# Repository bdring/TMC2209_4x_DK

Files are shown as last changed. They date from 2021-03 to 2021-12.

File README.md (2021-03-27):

## TMC2209 4 Axis Grbl_ESP32 CNC Controller

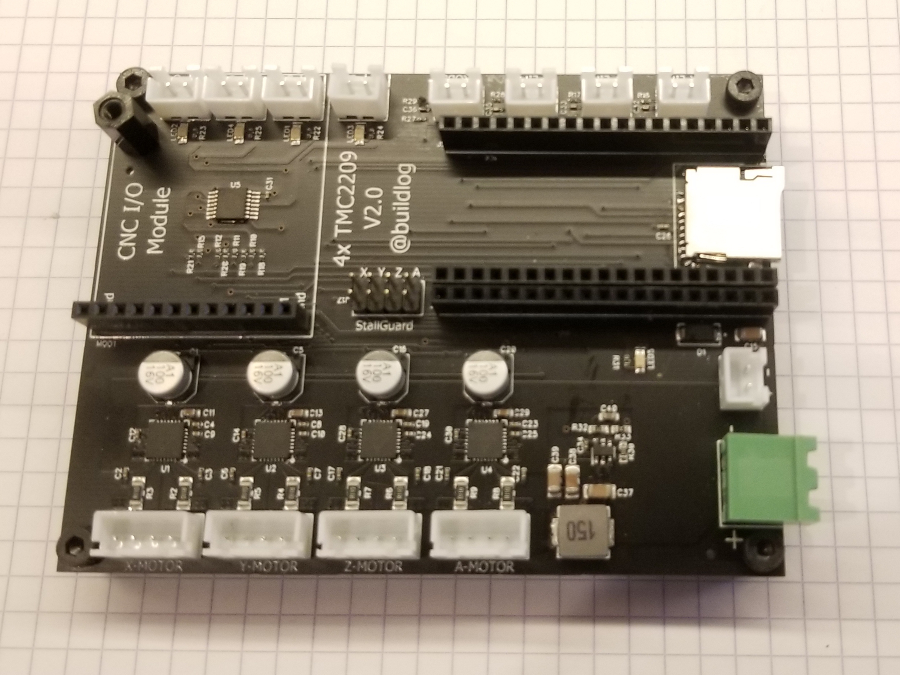
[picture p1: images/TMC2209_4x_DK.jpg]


This is a simple to set up and use CNC controller with 4 built in Trinamic TMC2209 stepper motor drivers. It is designed to run [Grbl_ESP32 firmware](https://github.com/bdring/Grbl_Esp32).

### Standard ESP32 Dev Kit Socket

The controller uses a standard ESP32 dev kit socket for module in the 2x19 format. It has an extra socket to allow the use of 0.9" wide and 1.0" wide versions.

### TMC2209 Drivers

These are very strong and super quiet stepper motor drivers. The firmware is in full control of the drivers. This allows you to set things like microstepping level and currents without jumpers and potentiometers. Sensorless end stops are supported. There are interactive tuning features to help set this up.

The 4 drivers can be set up for XYZA axes or any axis can be ganged for XYYZ type machines. 

### Inputs

There are 4 inputs. They are labeled for XY & Z limit limit switches and a probe, but they can be used for any type of input, such as XYZA or XYZ plus feed hold, etc.

### Outputs 

There are 4 outputs built into the controller. These are level shifted to 5V and can source or sink up to 25mA.  These can be used for spindle or laser PWMs. They can also be used to drive relay circuits. 

### CNC Output Modules.

The 4 outputs mentioned above are also wired to a standard CNC output module socket. This allows the use of many specialized modules, like RS485, 0-10V, Relays, High current MOSFETs, etc. This gives a lot of flexibility to this controller. Since the I/O for the modules is also wired to the built in outputs, you cannot use them independtly. 

Supported modules.

- [RS485 Modbus module for VFD spindles](https://github.com/bdring/6-Pack_CNC_Controller/wiki/RS485-Modbus-Module)
- [0-10V spindle module](https://github.com/bdring/6-Pack_CNC_Controller/wiki/0-10V-Output-Module)
- [Quad MOSFET module](https://github.com/bdring/6-Pack_CNC_Controller/wiki/Quad-MOSFET-Module)
- [Relay module](https://github.com/bdring/6-Pack_CNC_Controller/wiki/Relay-Module)
- [RC servo and BESC motor module](https://github.com/bdring/6-Pack_CNC_Controller/wiki/RC-Servo-BESC-CNC-I-O-Module)

### Micro SD Card

There is a micro SD socket. This allows gcode to be run without connected device.

### Laser Power Connector

There is a an extra connector that simply outputs the main power on a 2 terminal connector. This would typically used to power a low power laser module.

### Input Voltage

There is a pluggable terminal block for the input voltage. This is limited to 12V on version 2.0. Future versions will support 12V-24V.

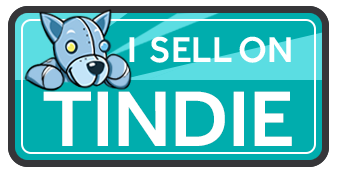
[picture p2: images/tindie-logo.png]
[](https://www.tindie.com/products/33366583/tmc2209-4-axis-grbl_esp32-cnc-controller/)

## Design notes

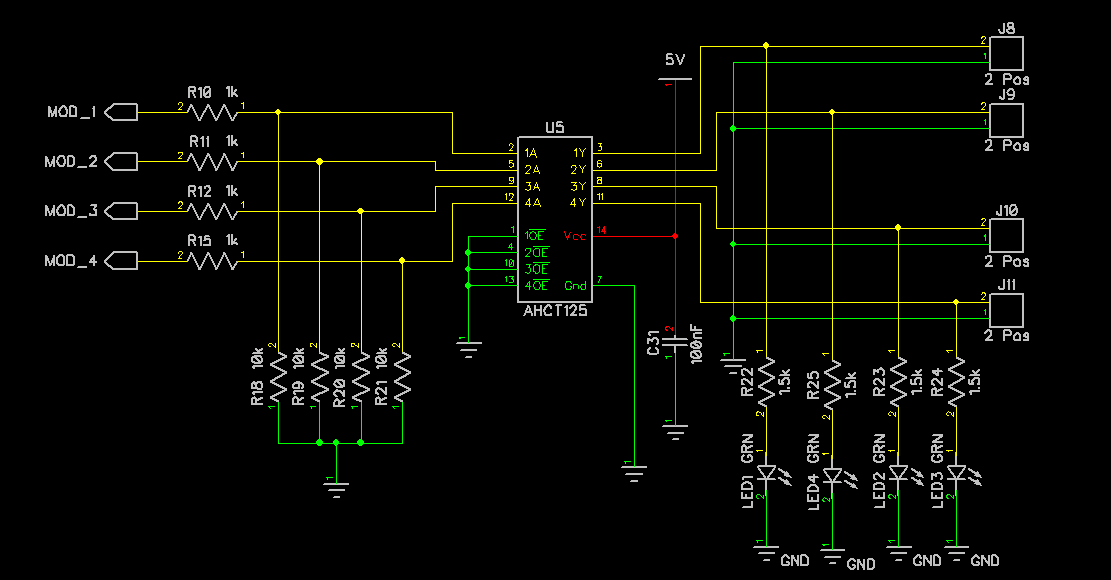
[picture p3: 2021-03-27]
images/5v_out_schematic.png

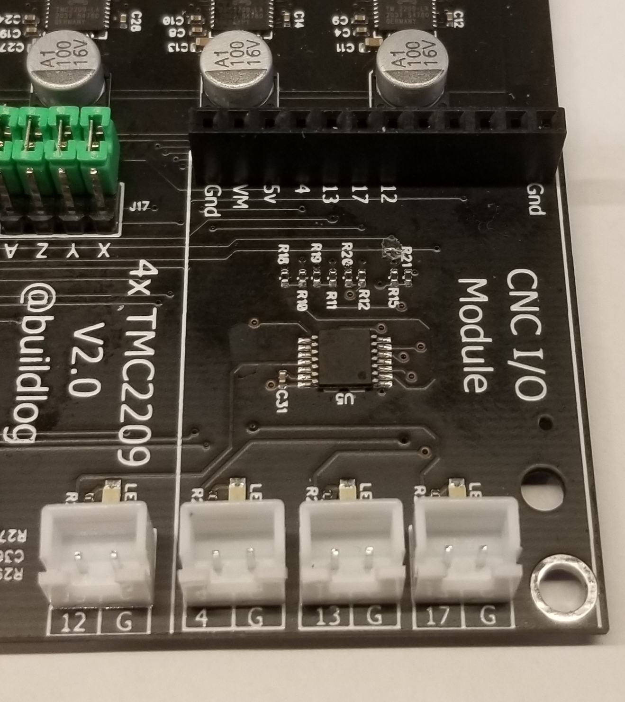
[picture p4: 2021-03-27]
images/output_pin_nums.jpg

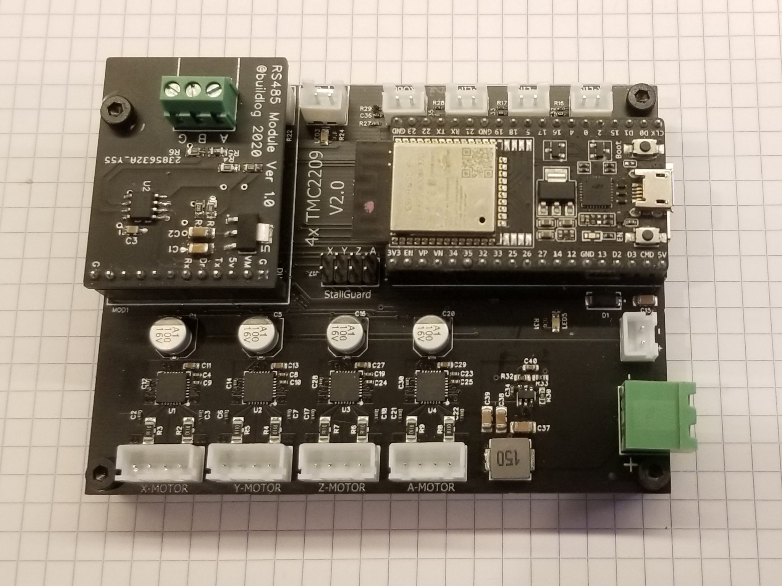
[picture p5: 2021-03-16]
images/TMC2209_4x_DK_Modules.jpg

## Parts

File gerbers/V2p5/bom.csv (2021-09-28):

RefDes | Quantity | Value | Name | Pattern | Manufacturer | MFG P/N | Source
C1, C5, C16, C20 | 4 | 100uF 35V | POL_100uF_35V EEEFK1V101XP | CaP_Elec_SMD_6.6x7.8 | PANASONIC | EEEFK1V101XP | https://lcsc.com/product-detail/Aluminum-Electrolytic-Capacitors-SMD_PANASONIC-EEEFK1V101XP_C178560.html
C2, C3, C4, C6, C7, C8, C12, C14, C17, C18, C19, C21, C22, C23, C26, C28, C30, C31, C32, C33, C34, C35, C36 | 23 | 100nF | NP_100nF_50V_0402 | CAP_0402_N | Samsung Electro-Mechanics | CL05B104KB54PNC | https://lcsc.com/product-detail/Others_Samsung-Electro-Mechanics_CL05B104KB54PNC_Samsung-Electro-Mechanics-CL05B104KB54PNC_C307331.html
C9, C10, C24, C25 | 4 | 22nF | NP_22nF_50V_0402 | CAP_0402_N | Samsung Electro-Mechanics | CL05B223KB5NNNC | https://lcsc.com/product-detail/Others_Samsung-Electro-Mechanics-CL05B223KB5NNNC_C337699.html
C11, C13, C27, C29 | 4 | 4.7uF | 4.7uF_25V_0603 | CAP_0603 | Samsung Electro-Mechanics | CL10A475KA8NQNC | https://lcsc.com/product-detail/Multilayer-Ceramic-Capacitors-MLCC-SMD-SMT_SAMSUNG_CL10A475KA8NQNC_4-7uF-475-10-25V_C69335.html
C15, C37 | 2 | 10uF 35V | NP_10uF_35V_1206 | CAP_1206 | Taiyo Yuden | GMK316BJ106KL-T | https://lcsc.com/product-detail/Multilayer-Ceramic-Capacitors-MLCC-SMD-SMT_Taiyo-Yuden-GMK316BJ106KL-T_C92797.html
C38, C39 | 2 | 22uF | NP_22uF_6.3V_1206 | CAP_1206 | Taiyo Yuden | JMK316BJ226KL-T | https://lcsc.com/product-detail/Multilayer-Ceramic-Capacitors-MLCC-SMD-SMT_TAIYO-YUDEN_JMK316BJ226KL-T_22uF-226-10-6-3V_C92791.html
C40 | 1 | 100pF | NP_100pF_50V_0603 | CAP_0603 | Walsin Tech Corp | 0603B101K500CT | https://lcsc.com/product-detail/Multilayer-Ceramic-Capacitors-MLCC-SMD-SMT_Walsin-Tech-Corp-0603B101K500_C123499.html
D1 | 1 | 40V 3A | Schottkey_40V_3A_DO-214AC | b340a-13-f | Diodes Incorporated | B340A-13-F | https://lcsc.com/product-detail/Schottky-Barrier-Diodes-SBD_DIODES_B340A-13-F_B340A-13-F_C85098.html
J1, J2, J6, J7 | 4 | 4P | XH-4A | B4B-XH-AM | BOOMELE(Boom Precision Elec) | C37815 | https://lcsc.com/product-detail/Wire-To-Board-Wire-To-Wire-Connector_BOOMELE-Boom-Precision-Elec-XH-4A_C37815.html
J3, J4, J5 | 3 | 19S | HDR Socket 1x19 0.1 | HDR-1x19 | Popular Products About LCSC | C319202 | https://lcsc.com/product-detail/Lack-of-specifications_BOOMELE-Boom-Precision-Elec-C319202_C319202.html
J8, J9, J10, J11, J12, J13, J14, J15, J16 | 9 | 2 Pos | B2B-XH-AM | B2B-XH-AM | JST | B2B-XH-AM(LF)(SN) | https://lcsc.com/product-detail/Wire-To-Board-Wire-To-Wire-Connector_JST-Sales-America-B2B-XH-AM-LF-SN_C161869.html
J17 | 1 | 2x4P | Header_2x4P | Header_2x4P 0.1 | Ckmtw(Shenzhen Cankemeng | C124386 | https://lcsc.com/product-detail/Pin-Header-Female-Header_Ckmtw-Shenzhen-Cankemeng-C124386_C124386.html
L1 | 1 | 15uH | 15uH_MWSA0603S | Inductor_MWSA0603S | Sunlord | MWSA0603S-150MT | https://lcsc.com/product-detail/Power-Inductors_Sunlord-MWSA0603S-150MT_C408452.html
LED1, LED2, LED3, LED4, LED5 | 5 | GRN | LED_GRN_0805 (Foshan) | LED_0805 | Foshan NationStar Optoelectronics | NCD0805G1 | https://lcsc.com/product-detail/Light-Emitting-Diodes-LED_Foshan-NationStar-Optoelectronics-NCD0805G1_C84260.html
MH1, MH2, MH3, MH4 | 4 |  | Mounting_hole_M3.7 | M4 Mounting Hole
MOD1 | 1 | 1x12 Socket | CNC_Module_Socket | CNC_Module_V3 | CJT(Changjiang Connectors) | A2541HWV-12P | https://lcsc.com/product-detail/Pin-Header-Female-Header_CJT-Changjiang-Connectors-A2541HWV-12P_C225509.html
R1, R13, R14, R18, R19, R20, R21, R26, R27 | 9 | 10k | 10k_0402 | RES_0402_N | YAGEO | RC0402FR-0710KL | https://lcsc.com/product-detail/Chip-Resistor-Surface-Mount_YAGEO-RC0402FR-0710KL_C60490.html
R2, R3, R4, R5, R6, R7, R8, R9 | 8 | 0.11R | 0.11R_1206 | RES_1206 | Uniroyal Elec | 1206W4F110LT5E | https://lcsc.com/product-detail/Chip-Resistor-Surface-Mount_UNI-ROYAL-Uniroyal-Elec-1206W4F110LT5E_C82532.html
R10, R11, R12, R15 | 4 | 1k | 1k_0402 | RES_0402_N | YAGEO | RC0402FR-071KL | https://lcsc.com/product-detail/Chip-Resistor-Surface-Mount_1KR-1001-1_C106235.html
R16, R17, R28, R29 | 4 | 100R | 100R_0402 | RES_0402_N | YAGEO | RC0402FR-07100RL | https://lcsc.com/product-detail/Chip-Resistor-Surface-Mount_YAGEO-RC0402FR-07100RL_C106232.html
R22, R23, R25, R31 | 4 | 1.5k | 1.5k_0402 | RES_0402_N | Uniroyal Elec | 0402WGF1501TCE | https://lcsc.com/product-detail/Chip-Resistor-Surface-Mount_Uniroyal-Elec-0402WGF1501TCE_C25867.html
R24 | 1 | 2.2k | 2.2k_0402 | RES_0402_N | Uniroyal Elec | 0402WGF2201TCE | https://lcsc.com/product-detail/Chip-Resistor-Surface-Mount_UNI-ROYAL-Uniroyal-Elec-0402WGF2201TCE_C25879.html
R30 | 1 | 510k | 510k_0603 | RES_0603 | YAGEO | RC0603FR-07510KL | https://lcsc.com/product-detail/Chip-Resistor-Surface-Mount_510KR-5103-1_C114066.html
R32 | 1 | 100k | 100k_0603 | RES_0603 | YAGEO | RC0603FR-07100KL | https://lcsc.com/product-detail/Chip-Resistor-Surface-Mount_YAGEO-RC0603FR-07100KL_C14675.html
R33 | 1 | 13.3k | 13.3k_0603 Uniroyal | RES_0603 | Uniroyal Elec | 0603WAF1332T5E | https://lcsc.com/product-detail/Chip-Resistor-Surface-Mount_Uniroyal-Elec-0603WAF1332T5E_C25952.html
SD1 | 1 | Micro SD | TF-01A | TF-01A_Rev2 | Korean Hroparts Elec | TF-01A | https://lcsc.com/product-detail/Card-Sockets-Connectors_Korean-Hroparts-Elec-TF-01A_C91145.html
TB1 | 1 | 2 Pos | TB_5p08mm_2POS Socket | TB_5mm_2POS | Ningbo Xinlaiya Elec. | XY2500R-D-5.08-2P | https://lcsc.com/product-detail/Pluggable-System-Terminal-Block_Ningbo-Xinlaiya-Elec-XY2500R-D-5-08-2P_C505824.html
U1, U2, U3, U4 | 4 | TMC2209 | TMC2209-LA (0.22mm) | TMC2209-LA (0.22mm) | Trinamic | TMC2209-LA | https://lcsc.com/product-detail/Motor-Drivers_TRINAMIC-Motion-Control-GmbH-TMC2209-LA_C465949.html
U5 | 1 | AHCT125 | AHCT125 | TSSOP-14 | Texas Instruments | SN74AHCT125PWR | https://lcsc.com/product-detail/Logic-Buffers-Drivers-Receivers-Transceivers_Texas-Instruments-Texas-Instruments-SN74AHCT125PWR_C36365.html
U6 | 1 | TPS54202 | TPS54202 | SOT23-THIN-6 | Texas Instruments | TPS54202HDDCR | https://lcsc.com/product-detail/Switching-Controllers_Texas-Instruments-Texas-Instruments-TPS54202HDDCR_C527684.html

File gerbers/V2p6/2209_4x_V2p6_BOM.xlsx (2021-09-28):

RefDes | Quantity | Qty SMT | Qty TH | Value | Name | Pattern | Manufacturer | MFG P/N | LCSC P/N | Source
C1, C5, C16, C20 | 4 | 4 |  | 100uF 35V | POL_100uF_35V EEEFK1V101XP | CaP_Elec_SMD_6.6x7.8 | PANASONIC | EEEFK1V101XP | C178560 | https://lcsc.com/product-detail/Aluminum-Electrolytic-Capacitors-SMD_PANASONIC-EEEFK1V101XP_C178560.html
C2, C3, C4, C6, C7, C8, C12, C14, C17, C18, C19, C21, C22, C23, C26, C28, C30, C31, C32, C33, C34, C35, C36 | 23 | 23 |  | 100nF | NP_100nF_50V_0402 | CAP_0402_N | Samsung Electro-Mechanics | CL05B104KB54PNC | C307331 | https://lcsc.com/product-detail/Others_Samsung-Electro-Mechanics_CL05B104KB54PNC_Samsung-Electro-Mechanics-CL05B104KB54PNC_C307331.html
C9, C10, C24, C25 | 4 | 4 |  | 22nF | NP_22nF_50V_0402 | CAP_0402_N | Samsung Electro-Mechanics | CL05B223KB5NNNC | C1532 | https://lcsc.com/product-detail/Others_Samsung-Electro-Mechanics-CL05B223KB5NNNC_C337699.html
C11, C13, C27, C29 | 4 | 4 |  | 4.7uF | 4.7uF_25V_0603 | CAP_0603 | Samsung Electro-Mechanics | CL10A475KA8NQNC | C69335 | https://lcsc.com/product-detail/Multilayer-Ceramic-Capacitors-MLCC-SMD-SMT_SAMSUNG_CL10A475KA8NQNC_4-7uF-475-10-25V_C69335.html
C15 | 1 | 1 |  | 10uF 35V | NP_10uF_35V_1206 | CAP_1206 | Taiyo Yuden | GMK316BJ106KL-T | C13585 | https://lcsc.com/product-detail/Multilayer-Ceramic-Capacitors-MLCC-SMD-SMT_Taiyo-Yuden-GMK316BJ106KL-T_C92797.html
C37, C38 | 2 | 2 |  | 2.2uF 50V | NP_2.2uF_50V_0805 | CAP_0805_N | Guangdong Fenghua Advanced Tech | 0805F225M500NT | C49217 | https://lcsc.com/product-detail/Multilayer-Ceramic-Capacitors-MLCC-SMD-SMT_FH-Guangdong-Fenghua-Advanced-Tech-0805F225M500NT_C49217.html
C39, C40 | 2 | 2 |  | 47uF 6.3V | NP_47uF_6.3V_0805 | CAP_0805_N | Samsung Electro-Mechanics | CL21A476MQYNNNE | C16780 | https://lcsc.com/product-detail/Multilayer-Ceramic-Capacitors-MLCC-SMD-SMT_SAMSUNG_CL21A476MQYNNNE_47uF-476-20-6-3V_C16780.html
C41 | 1 | 1 |  | 39pF 50V | NP_39pF_50V_0402 | CAP_0402_L | Yageo | CC0402JRNPO9BN390 | C106223 | https://lcsc.com/product-detail/Multilayer-Ceramic-Capacitors-MLCC-SMD-SMT_39pF-390-5-50V_C106223.html/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
C42 | 1 | 1 |  | 6.8nF 50V | NP_6.8nF_50V_0402 | CAP_0402_L | Guangdong Fenghua Advanced Tech | 0402B682K500NT | C1542 | https://lcsc.com/product-detail/Multilayer-Ceramic-Capacitors-MLCC-SMD-SMT_6-8nF-682-10-50V_C1542.html
D1 | 1 | 1 |  | 40V 3A | Schottkey_40V_3A_DO-214AC | b340a-13-f | Diodes Incorporated | B340A-13-F | C85098 | https://lcsc.com/product-detail/Schottky-Barrier-Diodes-SBD_DIODES_B340A-13-F_B340A-13-F_C85098.html
D2 | 1 | 1 |  | B560C | B560C | B560C | Diodes Incorporated | B560C-13-F | C85100 | https://www.lcsc.com/product-detail/Schottky-Barrier-Diodes-SBD_Diodes-Incorporated-B560CQ-13-F_C460781.html
J1, J2, J6, J7 | 4 |  | 4 | 4P | XH-4A | B4B-XH-AM | BOOMELE(Boom Precision Elec) | C37815 | C37815 | https://lcsc.com/product-detail/Wire-To-Board-Wire-To-Wire-Connector_BOOMELE-Boom-Precision-Elec-XH-4A_C37815.html
J3, J4, J5 | 3 |  | 3 | 19S | HDR Socket 1x19 0.1 | HDR-1x19 | Popular Products About LCSC | C319202 |  | https://lcsc.com/product-detail/Lack-of-specifications_BOOMELE-Boom-Precision-Elec-C319202_C319202.html
J8, J9, J10, J11, J12, J13, J14, J15, J16 | 9 |  | 9 | 2 Pos | B2B-XH-AM | B2B-XH-AM | JST | B2B-XH-AM(LF)(SN) | C161869 | https://lcsc.com/product-detail/Wire-To-Board-Wire-To-Wire-Connector_JST-Sales-America-B2B-XH-AM-LF-SN_C161869.html
J17 | 1 |  | 1 | 2x4P | Header_2x4P | Header_2x4P 0.1 | Ckmtw(Shenzhen Cankemeng | C124386 | C124386 | https://lcsc.com/product-detail/Pin-Header-Female-Header_Ckmtw-Shenzhen-Cankemeng-C124386_C124386.html
L1 | 1 | 1 |  | 10uH | 10uH_SMD_5.2x5.4 | MWSA0503S | Sunlord | MWSA0503S-100MT | C408408 | https://lcsc.com/product-detail/Power-Inductors_Sunlord-MWSA0503S-100MT_C408412.html
LED1, LED2, LED3, LED4, LED5 | 5 | 5 |  | GRN | LED_GRN_0805 (Foshan) | LED_0805 | Foshan NationStar Optoelectronics | NCD0805G1 | C188728 | https://lcsc.com/product-detail/Light-Emitting-Diodes-LED_Foshan-NationStar-Optoelectronics-NCD0805G1_C84260.html
MOD1 | 1 |  | 1 | 1x12 Socket | CNC_Module_Socket | CNC_Module_V3 | CJT(Changjiang Connectors) | A2541HWV-12P |  | https://lcsc.com/product-detail/Pin-Header-Female-Header_CJT-Changjiang-Connectors-A2541HWV-12P_C225509.html
R1, R14, R15, R18, R19, R20, R21, R26, R27 | 9 | 9 |  | 10k | 10k_0402 | RES_0402_N | YAGEO | RC0402FR-0710KL | C60490 | https://lcsc.com/product-detail/Chip-Resistor-Surface-Mount_YAGEO-RC0402FR-0710KL_C60490.html
R2, R3, R4, R5, R6, R7, R8, R9 | 8 | 8 |  | 0.11R | 0.11R_1206 | RES_1206 | Uniroyal Elec | 1206W4F110LT5E | C247458 | https://lcsc.com/product-detail/Chip-Resistor-Surface-Mount_UNI-ROYAL-Uniroyal-Elec-1206W4F110LT5E_C82532.html
R10, R11, R12, R13 | 4 | 4 |  | 1k | 1k_0402 | RES_0402_N | YAGEO | RC0402FR-071KL | C11702 | https://lcsc.com/product-detail/Chip-Resistor-Surface-Mount_1KR-1001-1_C106235.html
R16, R17, R28, R29 | 4 | 4 |  | 100R | 100R_0402 | RES_0402_N | YAGEO | RC0402FR-07100RL | C106232 | https://lcsc.com/product-detail/Chip-Resistor-Surface-Mount_YAGEO-RC0402FR-07100RL_C106232.html
R22, R23, R25, R31 | 4 | 4 |  | 1.5k | 1.5k_0402 | RES_0402_N | Uniroyal Elec | 0402WGF1501TCE | C25867 | https://lcsc.com/product-detail/Chip-Resistor-Surface-Mount_Uniroyal-Elec-0402WGF1501TCE_C25867.html
R24 | 1 | 1 |  | 2.2k | 2.2k_0402 | RES_0402_N | Uniroyal Elec | 0402WGF2201TCE | C25879 | https://lcsc.com/product-detail/Chip-Resistor-Surface-Mount_UNI-ROYAL-Uniroyal-Elec-0402WGF2201TCE_C25879.html
R30 | 1 | 1 |  | 270k | 270k_0402 | RES_0402_N | Uniroyal Elec | 0402WGF2703TCE | C25770 | https://lcsc.com/product-detail/Chip-Resistor-Surface-Mount_Uniroyal-Elec-0402WGF2703TCE_C25770.html/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
R32 | 1 | 1 |  | 100k | 100k_0402 | RES_0402_N | Uniroyal Elec | 0402WGF1003TCE | C25741 | https://lcsc.com/product-detail/Chip-Resistor-Surface-Mount_Uniroyal-Elec-0402WGF1003TCE_C25741.html/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
R33 | 1 | 1 |  | 13k | 13k_0402 | RES_0402_N | Uniroyal Elec | 0402WGF1302TCE | C25754 | https://lcsc.com/product-detail/Chip-Resistor-Surface-Mount_UNI-ROYAL-Uniroyal-Elec-0402WGF1302TCE_C25754.html
R34 | 1 | 1 |  | 51k | 51k_0402 | RES_0402_N | Uniroyal Elec | 0402WGF5102TCE | C25794 | https://lcsc.com/product-detail/Chip-Resistor-Surface-Mount_Uniroyal-Elec-0402WGF5102TCE_C25794.html/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
SD1 | 1 | 1 |  | Micro SD | TF-01A | TF-01A_Rev2 | Korean Hroparts Elec | TF-01A |  | https://lcsc.com/product-detail/Card-Sockets-Connectors_Korean-Hroparts-Elec-TF-01A_C91145.html
TB1 | 1 |  | 1 | 2 Pos | TB_5p08mm_2POS Socket | TB_5mm_2POS | Ningbo Xinlaiya Elec. | XY2500R-D-5.08-2P | C505824 | https://lcsc.com/product-detail/Pluggable-System-Terminal-Block_Ningbo-Xinlaiya-Elec-XY2500R-D-5-08-2P_C505824.html
U1, U2, U3, U4 | 4 | 4 |  | TMC2209 | TMC2209-LA (0.22mm) | TMC2209-LA (0.22mm) | Trinamic | TMC2209-LA | C465949 | https://lcsc.com/product-detail/Motor-Drivers_TRINAMIC-Motion-Control-GmbH-TMC2209-LA_C465949.html
U5 | 1 | 1 |  | AHCT125 | AHCT125 | TSSOP-14 | Texas Instruments | SN74AHCT125PWR | C36365 | https://lcsc.com/product-detail/Logic-Buffers-Drivers-Receivers-Transceivers_Texas-Instruments-Texas-Instruments-SN74AHCT125PWR_C36365.html
U6 | 1 | 1 |  | TPS54360 | TPS54360DDAR | TPS54360 | Texas Instruments | TPS54360DDAR | C44377 | https://lcsc.com/product-detail/DC-DC-Converters_Texas-Instruments-Texas-Instruments-TPS54360DDAR_C44377.html
 | Totals | 91 | 19 | 110
 | Unique | 27 | 6 | 33

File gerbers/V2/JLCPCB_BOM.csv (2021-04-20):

Comment | Designator | Footprint | LCSC Part#
100uF 35V | C1, C5, C16, C20 | CaP_Elec_SMD_6.6x7.8 | C178560
100nF | C2, C3, C4, C6, C7, C8, C12, C14, C17, C18, C19, C21, C22, C23, C26, C28, C30, C31, C32, C33, C34, C35, C36 | CAP_0402_N | C307331
22nF | C9, C10, C24, C25 | CAP_0402_N | C1532
4.7uF | C11, C13, C27, C29 | CAP_0603 | C69335
10uF 35V | C15, C37 | CAP_1206 | C13585
22uF | C38, C39 | CAP_1206 | C90146
100pF | C40 | CAP_0603 | C14858
40V 3A | D1 | b340a-13-f | C85098
4P | J1, J2, J6, J7 | B4B-XH-AM | C37815
19S | J3, J4, J5 | HDR-1x19
2 Pos | J8, J9, J10, J11, J12, J13, J14, J15, J16 | B2B-XH-AM | C161869
2x4P | J17 | Header_2x4P 0.1
15uH | L1 | Inductor_MWSA0603S | C408452
GRN | LED1, LED2, LED3, LED4, LED5 | LED_0805 | C188728
 | MH1, MH2, MH3, MH4 | M4 Mounting Hole
1x12 Socket | MOD1 | CNC_Module_V3
10k | R1, R13, R14, R18, R19, R20, R21, R26, R27 | RES_0402_N | C60490
0.11R | R2, R3, R4, R5, R6, R7, R8, R9 | RES_1206 | C247458
1k | R10, R11, R12, R15 | RES_0402_N | C11702
100R | R16, R17, R28, R29 | RES_0402_N | C106232
1.5k | R22, R23, R24, R25, R31 | RES_0402_N | C25867
510k | R30 | RES_0603 | C23192
100k | R32 | RES_0603 | C25803
13.3k | R33 | RES_0603 | C25952
Micro SD | SD1 | TF-01A_Rev2
2 Pos | TB1 | TB_5mm_2POS | C505824
TMC2209 | U1, U2, U3, U4 | TMC2209-LA (0.22mm) | C465949
AHCT125 | U5 | TSSOP-14 | C36365
TPS54202 | U6 | SOT23-THIN-6 | C134129

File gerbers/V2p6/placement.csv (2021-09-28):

RefDes | Origin X (mm) | Origin Y (mm) | Side | Rotate
C1 | 13.411 | 26.899 | Top | 90.0
C2 | 8.3 | 13.5 | Top | 90.0
C3 | 18.8 | 13.5 | Top | 90.0
C4 | 17.551 | 20.345 | Top | 0.0
C5 | 28.5 | 26.899 | Top | 90.0
C6 | 23.2 | 13.5 | Top | 90.0
C7 | 34 | 13.5 | Top | 90.0
C8 | 32.5 | 20.32 | Top | 0.0
C9 | 17.704 | 18.986 | Top | 180.0
C10 | 32.677 | 18.986 | Top | 180.0
C11 | 16.447 | 21.971 | Top | 180.0
C12 | 9.385 | 18.872 | Top | 90.0
C13 | 31.725 | 21.895 | Top | 180.0
C14 | 24.362 | 18.872 | Top | 90.0
C15 | 96.41 | 33.496 | Top | 180.0
C16 | 43.5 | 26.899 | Top | 90.0
C17 | 38.1 | 13.5 | Top | 90.0
C18 | 49.1 | 13.5 | Top | 90.0
C19 | 47.4 | 20.32 | Top | 0.0
C20 | 58.5 | 26.899 | Top | 90.0
C21 | 53.2 | 13.5 | Top | 90.0
C22 | 63.95 | 13.5 | Top | 90.0
C23 | 62.5 | 20.32 | Top | 0.0
C24 | 47.654 | 18.948 | Top | 180.0
C25 | 62.665 | 18.986 | Top | 180.0
C26 | 84.138 | 49.847 | Top | 0.0
C27 | 46.344 | 21.971 | Top | 180.0
C28 | 39.224 | 19.025 | Top | 90.0
C29 | 60.86 | 21.971 | Top | 180.0
C30 | 54.298 | 18.872 | Top | 90.0
C31 | 24.632 | 54.609 | Top | 90.0
C32 | 81.598 | 69.056 | Top | 180.0
C33 | 70.485 | 69.215 | Top | 180.0
C34 | 75.406 | 8.731 | Top | 0.0
C35 | 58.572 | 68.739 | Top | 180.0
C36 | 47.308 | 68.739 | Top | 180.0
C37 | 69.056 | 5.874 | Top | 0.0
C38 | 69.056 | 7.779 | Top | 0.0
C39 | 70.009 | 17.462 | Top | 0.0
C40 | 70.009 | 19.367 | Top | 0.0
C41 | 80.9 | 4.6 | Top | 180.0
C42 | 82.4 | 5.039 | Top | 90.0
D1 | 88.975 | 33.496 | Top | 180.0
D2 | 75.406 | 12.224 | Top | 180.0
J1 | 13.5 | 4.5 | Top | 0.0
J2 | 28.5 | 4.5 | Top | 0.0
J3 | 75.16 | 37.601 | Top | 180.0
J4 | 75.16 | 40.141 | Top | 180.0
J5 | 75.16 | 63.001 | Top | 180.0
J6 | 43.5 | 4.5 | Top | 0.0
J7 | 58.5 | 4.5 | Top | 0.0
J8 | 28.099 | 70.365 | Top | 180.0
J9 | 19.366 | 70.365 | Top | 180.0
J10 | 10.954 | 70.365 | Top | 180.0
J11 | 37.941 | 70.365 | Top | 180.0
J12 | 86.995 | 70.365 | Top | 180.0
J13 | 75.565 | 70.365 | Top | 180.0
J14 | 64.135 | 70.365 | Top | 180.0
J15 | 52.705 | 70.365 | Top | 180.0
J16 | 95.25 | 26.511 | Top | 90.0
J17 | 43.454 | 38.735 | Top | 0.0
L1 | 75.556 | 18.256 | Top | 180.0
LED1 | 28.099 | 64.556 | Top | 90.0
LED2 | 10.954 | 64.77 | Top | 90.0
LED3 | 37.783 | 64.556 | Top | 90.0
LED4 | 19.526 | 64.77 | Top | 90.0
LED5 | 80.416 | 30.028 | Top | 90.0
MOD1 | 16.669 | 34.981 | Top | 180.0
R1 | 57.944 | 60.801 | Top | 0.0
R2 | 16.8 | 10.8 | Top | 90.0
R3 | 10.2 | 10.8 | Top | 90.0
R4 | 31.761 | 10.8 | Top | 90.0
R5 | 25.264 | 10.8 | Top | 90.0
R6 | 46.781 | 10.8 | Top | 90.0
R7 | 40.213 | 10.8 | Top | 90.0
R8 | 61.724 | 10.8 | Top | 90.0
R9 | 55.258 | 10.8 | Top | 90.0
R10 | 23.002 | 45.466 | Top | 270.0
R11 | 20.462 | 45.466 | Top | 270.0
R12 | 18.012 | 45.466 | Top | 270.0
R13 | 15.304 | 45.466 | Top | 270.0
R14 | 81.598 | 67.628 | Top | 0.0
R15 | 70.485 | 67.786 | Top | 0.0
R16 | 81.598 | 70.168 | Top | 0.0
R17 | 70.485 | 70.365 | Top | 0.0
R18 | 24.5 | 45.466 | Top | 90.0
R19 | 21.813 | 45.466 | Top | 90.0
R20 | 19.162 | 45.466 | Top | 90.0
R21 | 14.125 | 45.466 | Top | 90.0
R22 | 30.004 | 64.815 | Top | 270.0
R23 | 12.7 | 64.815 | Top | 270.0
R24 | 39.529 | 64.815 | Top | 270.0
R25 | 21.114 | 64.815 | Top | 270.0
R26 | 58.572 | 67.577 | Top | 0.0
R27 | 47.308 | 67.151 | Top | 0.0
R28 | 58.572 | 70.365 | Top | 0.0
R29 | 47.308 | 70.107 | Top | 0.0
R30 | 76.835 | 2.381 | Top | 180.0
R31 | 78.511 | 30.028 | Top | 270.0
R32 | 73.5 | 2.4 | Top | 180.0
R33 | 80.9 | 5.5 | Top | 180.0
R34 | 78.899 | 2.381 | Top | 180.0
SD1 | 93.345 | 51.349 | Top | 180.0
TB1 | 93.219 | 10.153 | Top | 90.0
U1 | 13.5 | 18.1 | Top | 180.0
U2 | 28.5 | 18.1 | Top | 180.0
U3 | 43.454 | 18.1 | Top | 180.0
U4 | 58.454 | 18.1 | Top | 180.0
U5 | 19.567 | 53.122 | Top | 0.0
U6 | 75.556 | 5.715 | Top | 270.0

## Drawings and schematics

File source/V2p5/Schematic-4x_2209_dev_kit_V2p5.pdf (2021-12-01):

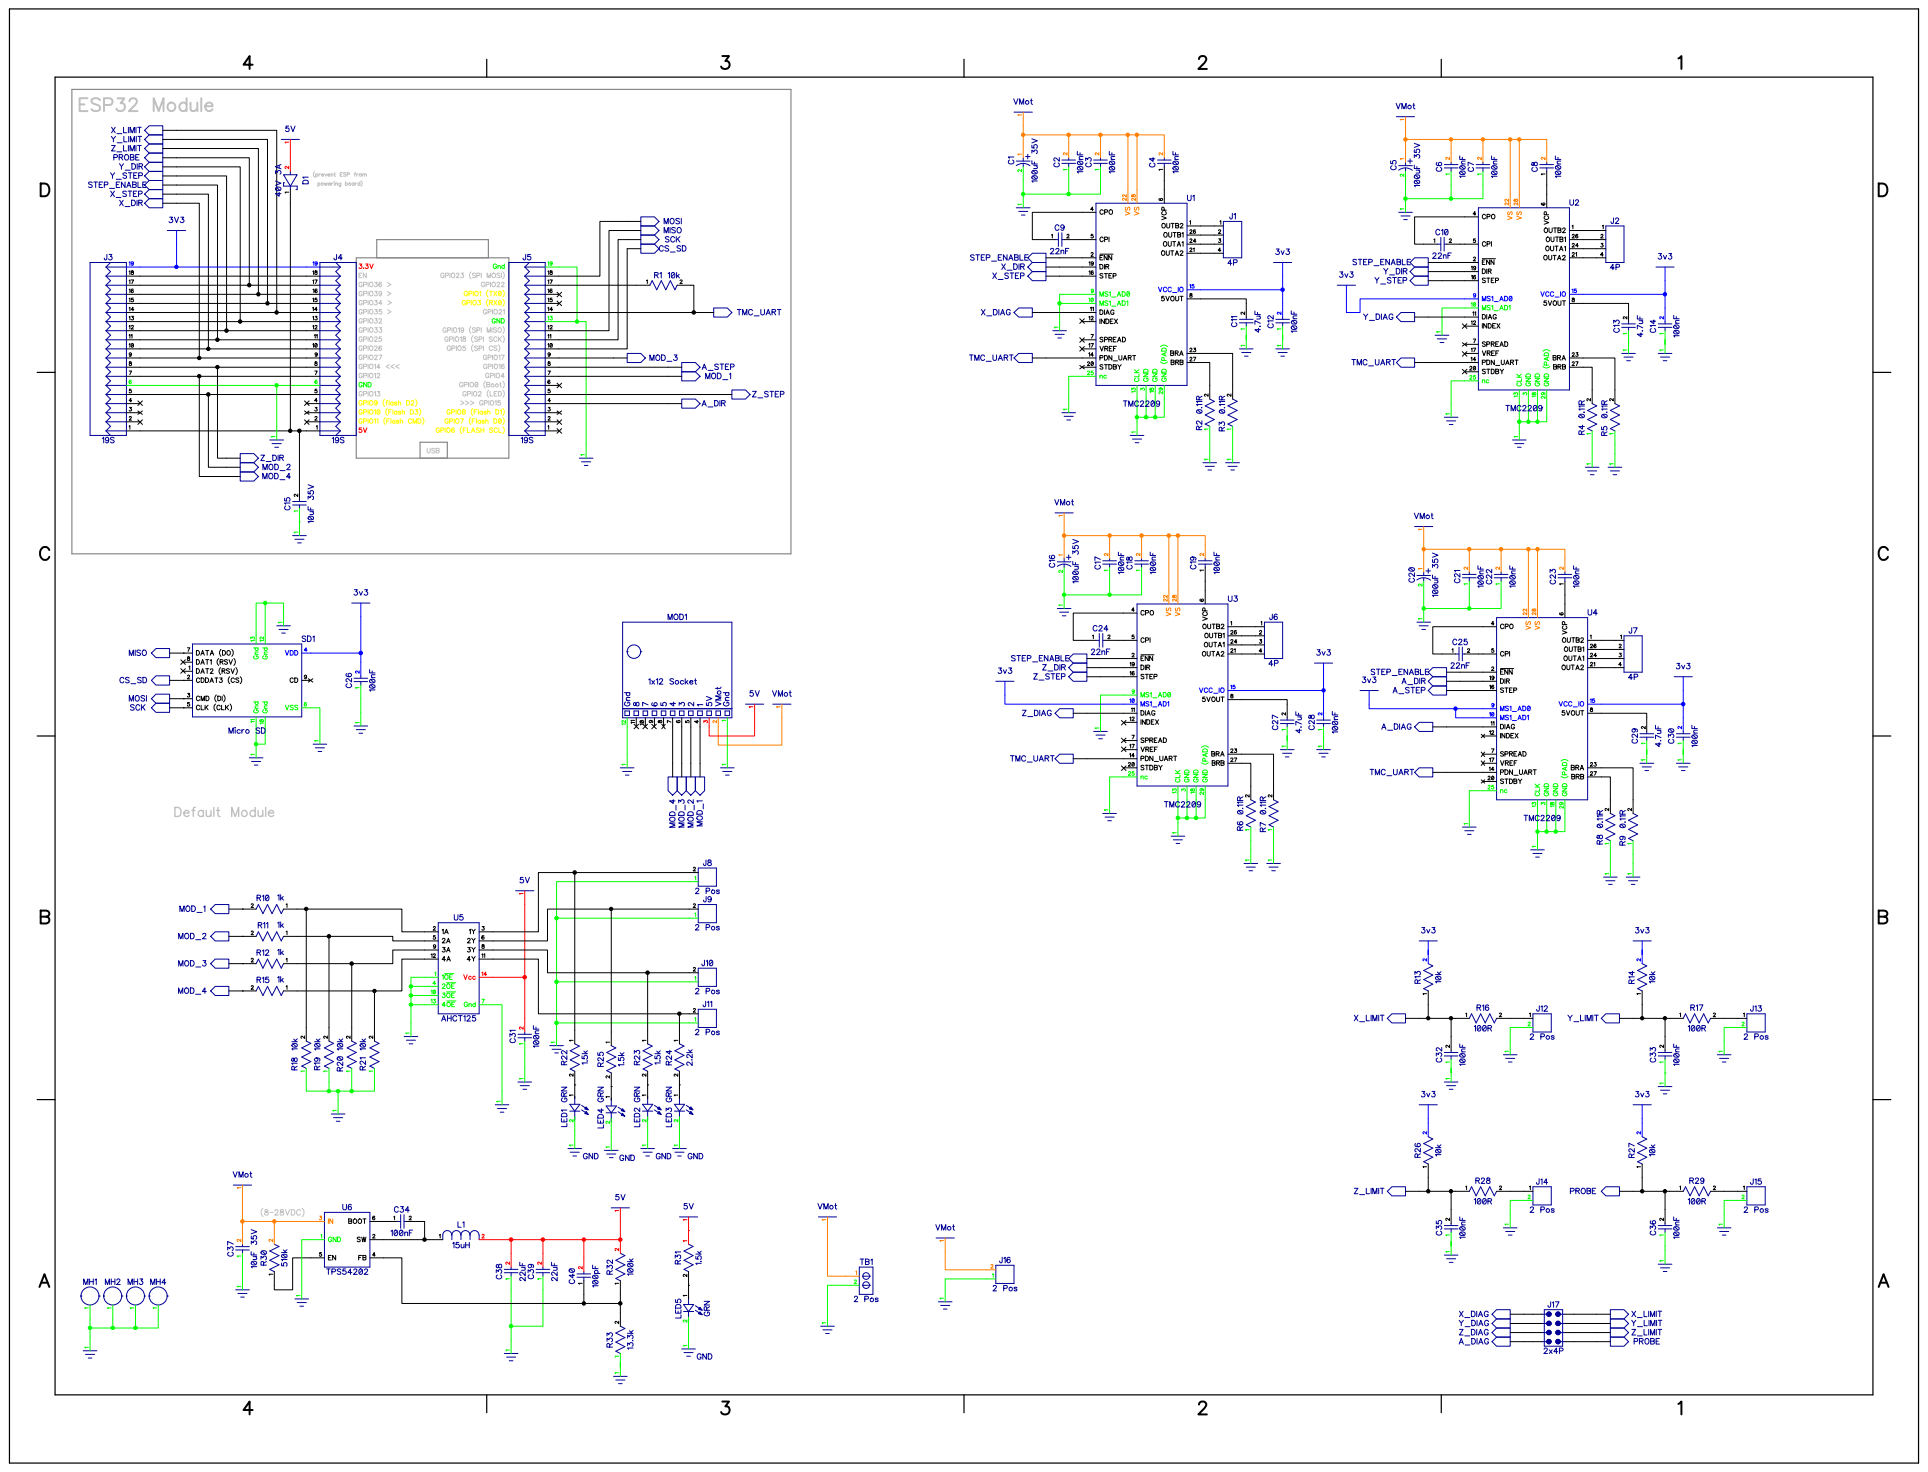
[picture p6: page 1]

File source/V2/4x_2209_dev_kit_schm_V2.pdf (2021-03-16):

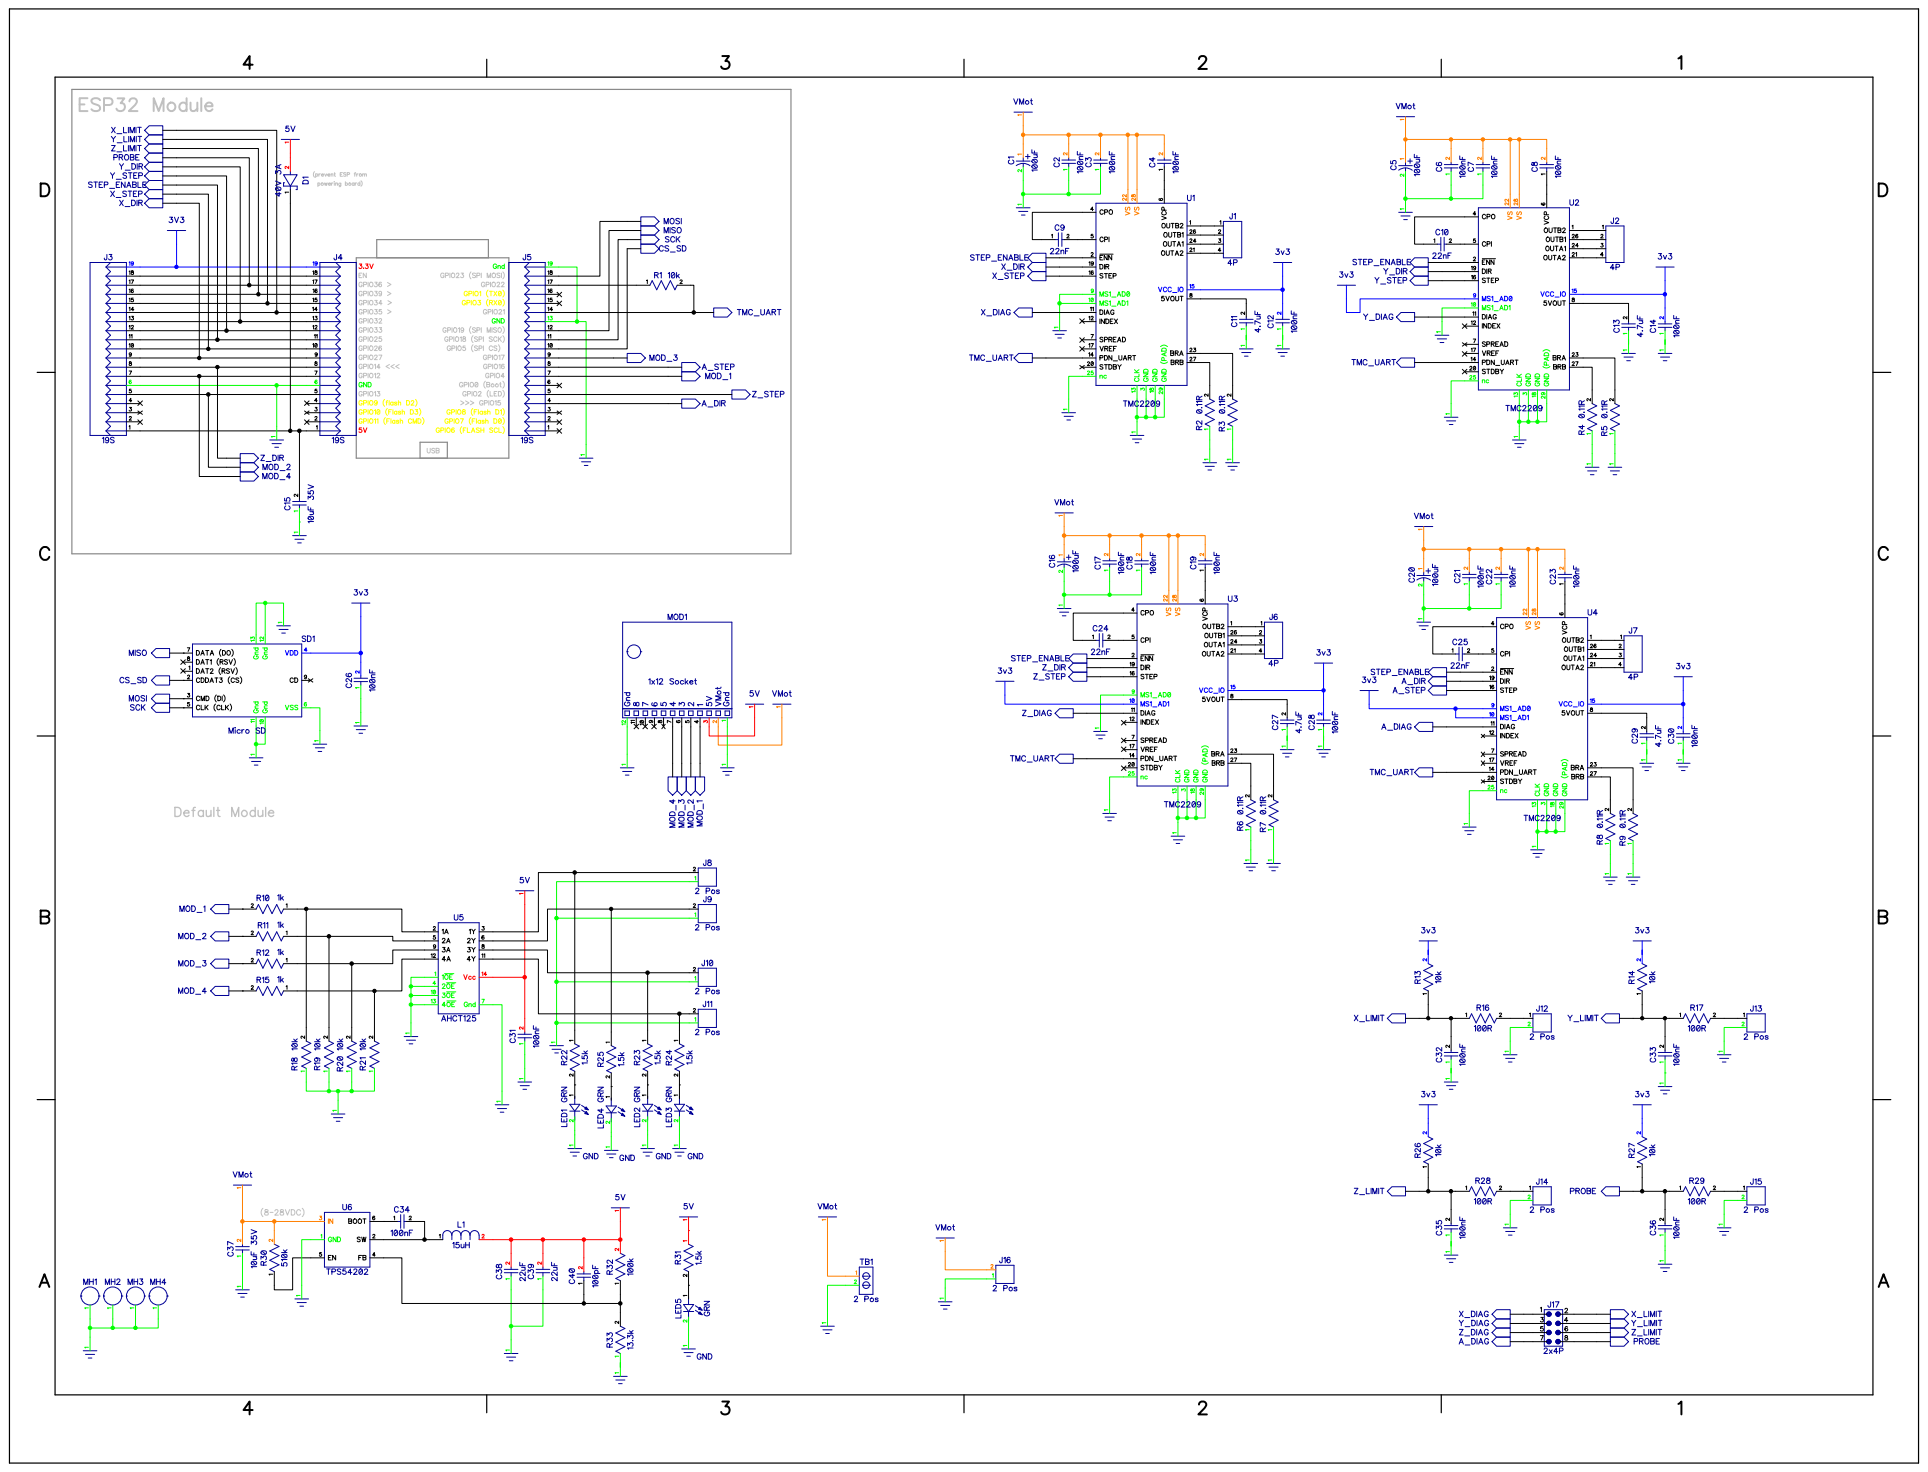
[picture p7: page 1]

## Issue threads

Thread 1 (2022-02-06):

Issues with SD card showing

blackpressinc, 2022-02-06:
I have inserted a 4gb, FAT32 formatted SD card into the SD card slot but when using fluidnc and clicking the "SD" card button, I get the following error on the serial console

ERROR:20
Unsupported or invalid g-code command found in block.

I noticed a similar issue for the FluidNC repository (https://github.com/bdring/FluidNC/issues/115)

The solution there appeared to be something to do with the "card detection pin" I believe defined in the yaml file. I noticed even on the test_drive_SD.yaml the following SD card configuration

sdcard:
  card_detect_pin: NO_PIN
  cs_pin: gpio.5

For the TMC2209_4x_DK board, is there an appropriate card detect pin? Is there some other issue that might be occurring here?

blackpressinc, 2022-02-06:
It seems the issue has been resolved. It might have been uploading a correct .yaml configuration or something else but now I can read the SD card and everything is working.

Closed 2022-02-06.

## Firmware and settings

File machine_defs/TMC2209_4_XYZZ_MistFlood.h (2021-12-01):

#pragma once
// clang-format off

/*
    TMC2209_4_XYZZ_MistFlood.h

    2020-10-25 B. Dring for Kent Deemter

    This is a machine definition file to use the FYSTEC E4 3D Printer controller
    This is a 4 motor controller. This is setup for XYZA, but XYYZ, could also be used.
    There are 5 inputs
    The controller has outputs for a Fan, Hotbed and Extruder. There are mapped to
    spindle, mist and flood coolant to drive an external relay.

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
    You should have received a copy of the GNU General Public License
    along with Grbl_ESP32.  If not, see <http://www.gnu.org/licenses/>.
*/

#define MACHINE_NAME            "TMC2209 4x XYZZ"

#define N_AXIS 3

#define TRINAMIC_UART_RUN_MODE       TrinamicUartMode :: StealthChop
#define TRINAMIC_UART_HOMING_MODE    TrinamicUartMode :: StealthChop

#define TMC_UART                UART_NUM_1
#define TMC_UART_RX             GPIO_NUM_21
#define TMC_UART_TX             GPIO_NUM_22   

#define X_TRINAMIC_DRIVER       2209
#define X_STEP_PIN              GPIO_NUM_26
#define X_DIRECTION_PIN         GPIO_NUM_27
#define X_RSENSE                TMC2209_RSENSE_DEFAULT
#define X_DRIVER_ADDRESS        0
#define DEFAULT_X_MICROSTEPS    16

#define Y_TRINAMIC_DRIVER       2209
#define Y_STEP_PIN              GPIO_NUM_33
#define Y_DIRECTION_PIN         GPIO_NUM_32
#define Y_RSENSE                TMC2209_RSENSE_DEFAULT
#define Y_DRIVER_ADDRESS        1
#define DEFAULT_Y_MICROSTEPS    16

#define Z_TRINAMIC_DRIVER       2209
#define Z_STEP_PIN              GPIO_NUM_2
#define Z_DIRECTION_PIN         GPIO_NUM_14
#define Z_RSENSE                TMC2209_RSENSE_DEFAULT
#define Z_DRIVER_ADDRESS        2
#define DEFAULT_Z_MICROSTEPS    16

#define Z2_TRINAMIC_DRIVER       2209
#define Z2_STEP_PIN              GPIO_NUM_16
#define Z2_DIRECTION_PIN         GPIO_NUM_15
#define Z2_RSENSE                TMC2209_RSENSE_DEFAULT
#define Z2_DRIVER_ADDRESS        3
#define DEFAULT_Z2_MICROSTEPS    16

#define X_LIMIT_PIN             GPIO_NUM_35
#define Y_LIMIT_PIN             GPIO_NUM_34
#define Z_LIMIT_PIN             GPIO_NUM_39
#define Z2_LIMIT_SWITCH         GPIO_NUM_36

// OK to comment out to use pin for other features
#define STEPPERS_DISABLE_PIN    GPIO_NUM_25

#define COOLANT_MIST_PIN        GPIO_NUM_12
#define COOLANT_FLOOD_PIN       GPIO_NUM_4
#define USER_DIGITAL_PIN_0      GPIO_NUM_13
#define USER_DIGITAL_PIN_1      GPIO_NUM_17

// ===================== defaults ======================
// https://github.com/bdring/Grbl_Esp32/wiki/Setting-Defaults

#define DEFAULT_INVERT_PROBE_PIN 1

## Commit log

2021-03-16 Adding files
    [2209_4x_Module_V2_BOM.xlsx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]
2021-03-16 adding schematic PDF

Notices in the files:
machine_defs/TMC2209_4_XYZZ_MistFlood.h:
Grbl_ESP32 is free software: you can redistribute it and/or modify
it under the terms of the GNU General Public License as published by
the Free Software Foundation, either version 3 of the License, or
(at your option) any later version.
